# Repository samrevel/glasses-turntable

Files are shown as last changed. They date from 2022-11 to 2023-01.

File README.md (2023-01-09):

# glasses-turntable
This repository has the code, schematic, board. etc for the electronics of the glasses turntable kiosk display in Revel Digital warehouse 13.

The glasses turntable electronics board (board) uses a ATmega8 microcontroller to controll a H bridge that controlls a brushed DC motor. The DC motor has a gear boc to slow the motor down and to increase torqu. The motor turns the whole display. The display is ran from a 12V dc source and is fused. All the logic on the board is running 5V.

On the board there are connector for LEDs (12V LED string), power (2.1X5.5mm barrel jack center positive 12V), homing switch, extranal button (not used), mbrushed DC motor, serial, programmer conncetor, and fan (12V power out, not used). 

The display will rotate when the board recives a serial command. There serial commands are sent by a display located need the glasses turntable. When the board recives a command it will return the same serial command back.

Serial settings:
- Buad: 9600
- Bits: 8
- Stop Bits: 1
- Parity: None
- Flow Control: None
- Data format: ASCII
- Ending charachers: None (will not hurt if send it)

Serial commands (in ASCII):
- "1" rotate to side 1
- "2" rotate to side 2
- "3" rotate to side 3
- "4" rotate for about a second
- "5" rotate for about a second backwares
- "6" rotate for about a haft second
- "7" rotate for about a haft backwares

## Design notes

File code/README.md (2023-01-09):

This the code for the glasses turntable. The code is for the ATmega8 microcontroller located on the PCB. The ATmega8 is running at 8MHz using a extranl resonator.

The code was writen as a PlatformIO project written all in C with no frameworks. Located here is the soucre folder with the code and the PlatformIO Project Configuration File.

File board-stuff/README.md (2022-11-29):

This is all the file that is use to design the electrionics. Everything was make using KiCad and left all the KiCad project file. 
There is also a PDF of the schematic so you can look at it if you dont have KiCad. There are the PCB gerber files too.

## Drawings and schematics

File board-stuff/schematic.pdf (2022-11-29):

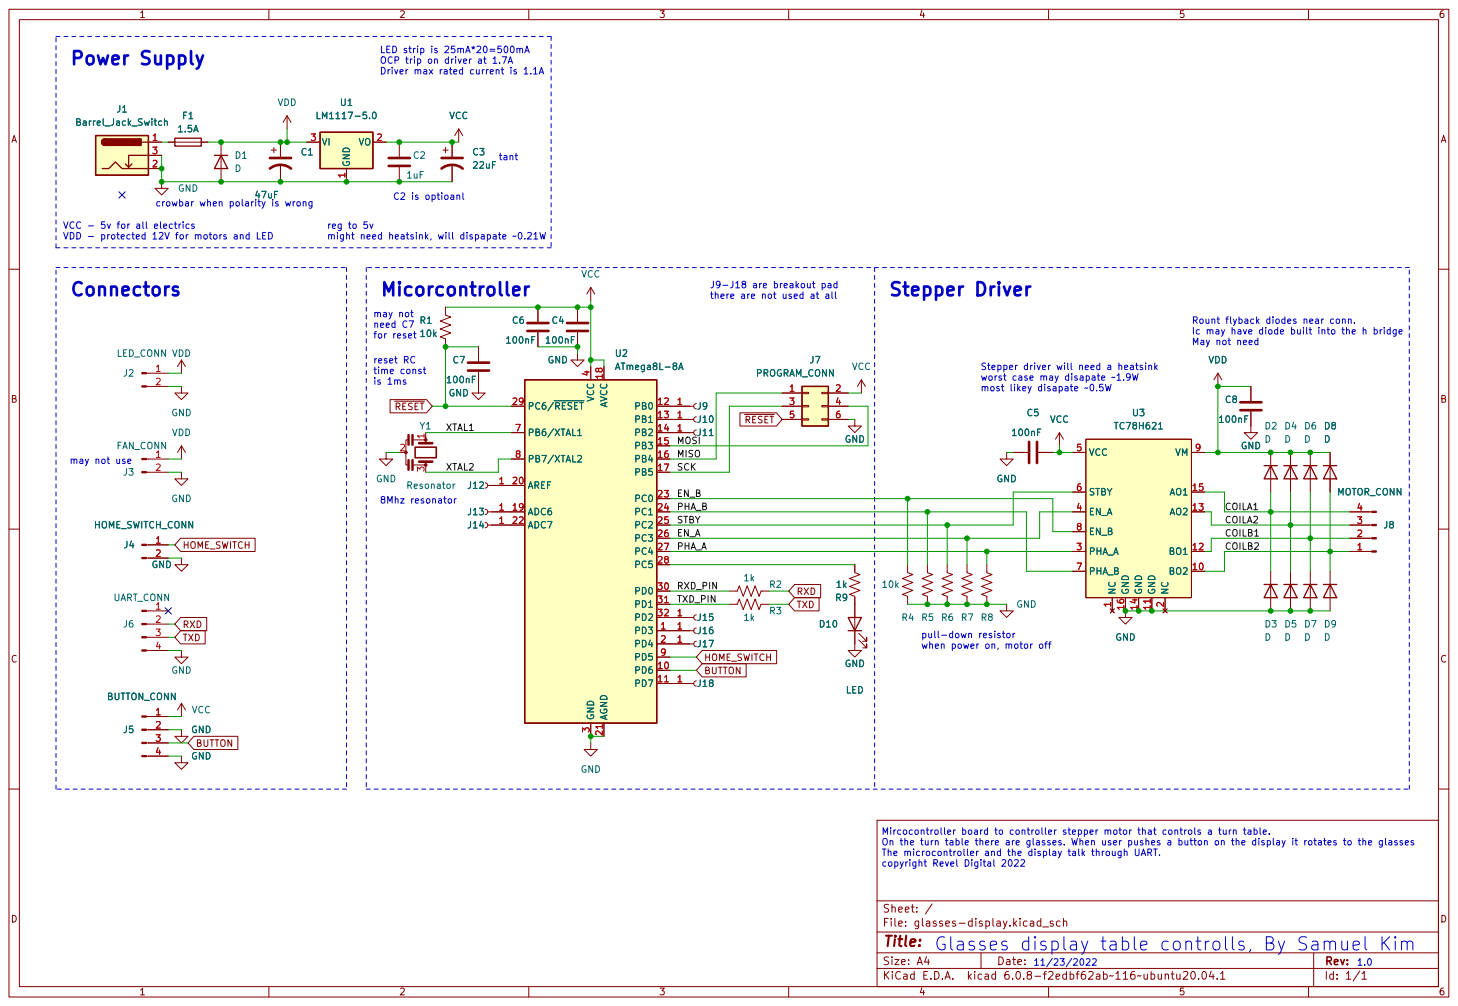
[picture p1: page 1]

for reset LED strip is 25mA*20=500mA
OCP trip on driver at 1.7A Driver max rated current is 1.1A
LM1117-5.0 GND

crowbar when polarity is wrong

VCC - 5v for all electrics VDD - protected 12V for motors and LED

reg to 5v
might need heatsink, will dispapate ~0.21W

1.0 Stepper Driver J9-J18 are breakout pad

Rount flyback diodes near conn. Ic may have diode built into the h bridge VDD

worst case may disapate ~1.9W
most likey disapate ~0.5W

2 PHA_A 3 EN_A 4 VCC 5 STBY 6 PHA_B 7 EN_B 8 VM 9 U3 TC78H621 VCC GND

2 PHA_A 3 EN_A 4 VCC 5 STBY 6 PHA_B 7 EN_B 8 VM 9 GND

1 BO2 10 GND 11 BO1 12 AO2 13 GND 14 AO1 15 GND 16 NC

pull-down resistor
when power on, motor off 11/23/2022 Glasses display table controlls, By Samuel Kim

On the turn table there are glasses. When user pushes a button on the display it rotates to the glasses
The microcontroller and the display talk through UART.
copyright Revel Digital 2022

File: glasses-display.kicad_sch Sheet: /
Id: 1/1 Title:

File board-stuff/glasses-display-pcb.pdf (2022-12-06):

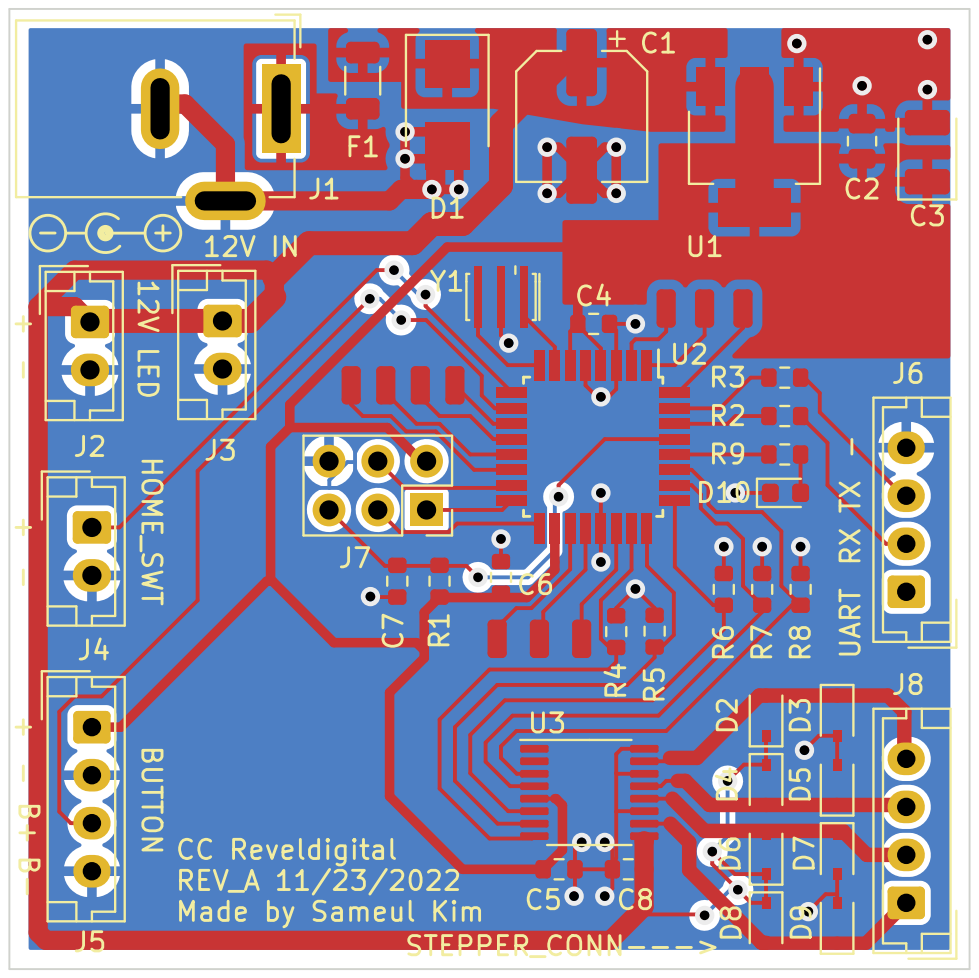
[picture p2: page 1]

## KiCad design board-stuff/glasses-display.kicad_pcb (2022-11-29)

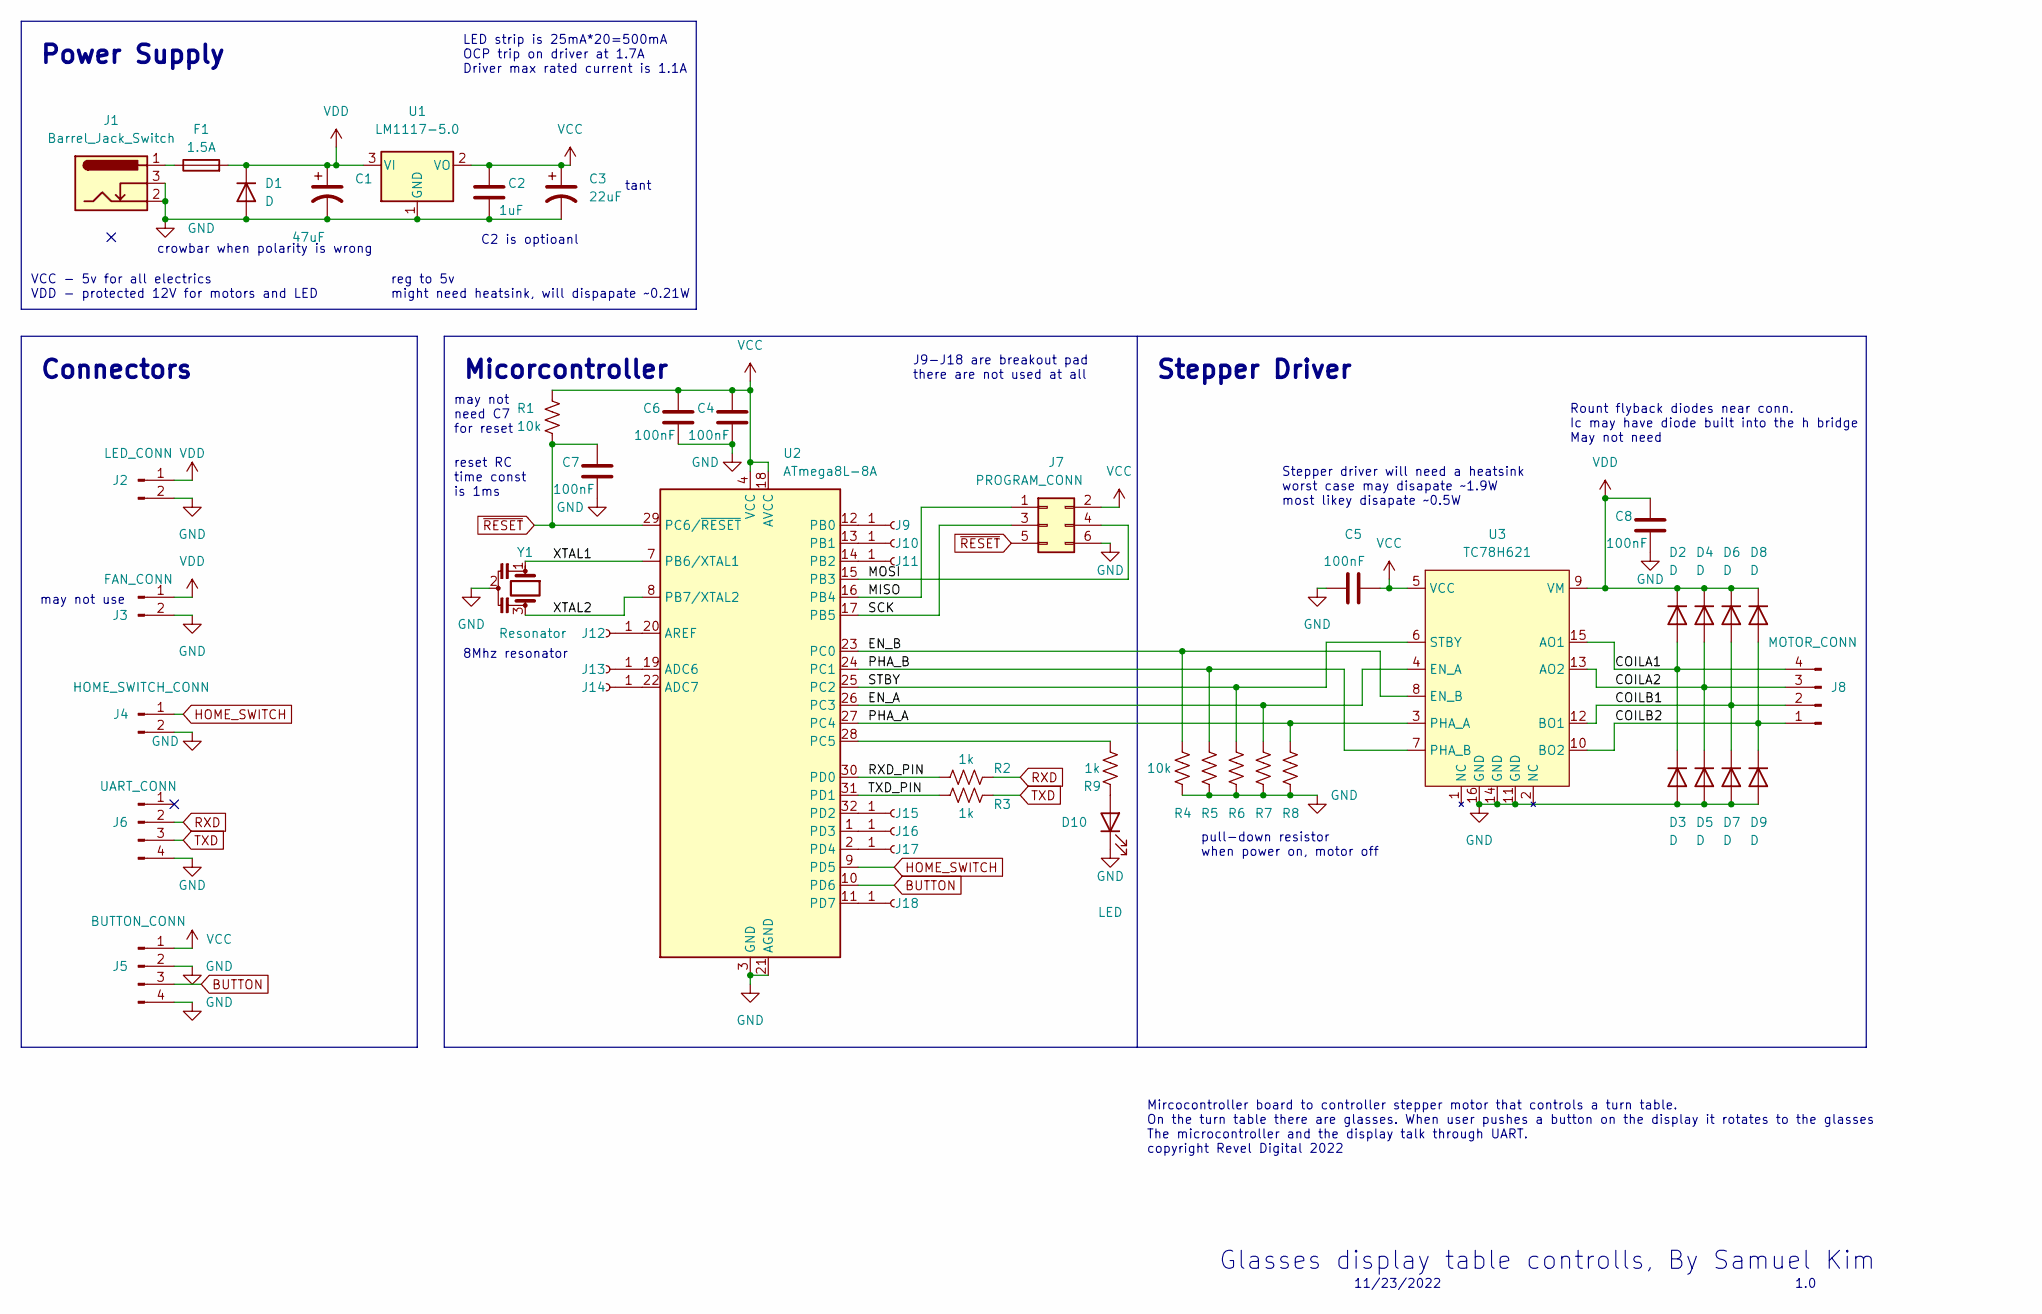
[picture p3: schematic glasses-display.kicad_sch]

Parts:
C1: 47uF; CP_Elec_6.3x5.2
C2: 1uF; R_0805_2012Metric
C3: 22uF; CP_EIA-3528-12_Kemet-T
C4, C5, C6, C7, C8: 100nF; R_0603_1608Metric
D1: D; D_SMB
D2, D3, D4, D5, D6, D7, D8, D9: D; D_SOD-323
D10: LED; LED_0603_1608Metric
F1: 1.5A; R_1206_3216Metric
J1: Barrel_Jack_Switch; BarrelJack_GCT_DCJ200-10-A_Horizontal
J2: LED_CONN; JST_EH_B2B-EH-A_1x02_P2.50mm_Vertical
J3: FAN_CONN; JST_EH_B2B-EH-A_1x02_P2.50mm_Vertical
J4: HOME_SWITCH_CONN; JST_EH_B2B-EH-A_1x02_P2.50mm_Vertical
J5: BUTTON_CONN; JST_EH_B4B-EH-A_1x04_P2.50mm_Vertical
J6: UART_CONN; JST_EH_B4B-EH-A_1x04_P2.50mm_Vertical
J7: PROGRAM_CONN; PinSocket_2x03_P2.54mm_Vertical
J8: MOTOR_CONN; JST_EH_B4B-EH-A_1x04_P2.50mm_Vertical
J9, J10, J11, J12, J13, J14, J15, J16, J17, J18: PAD; SolderWirePad_1x01_SMD_1x2mm
R1, R4, R5, R6, R7, R8: 10k; R_0603_1608Metric
R2, R3, R9: 1k; R_0603_1608Metric
U1: LM1117-5.0; SOT-223-3_TabPin2
U2: ATmega8L-8A; TQFP-32_7x7mm_P0.8mm
U3: TC78H621; TSSOP-16_4.4x5mm_P0.65mm
Y1: Resonator; Resonator_SMD_Murata_CSTxExxV-3Pin_3.0x1.1mm_HandSoldering

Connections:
/COILA1: D2.2 (A), D3.1 (K), J8.4, U3.15 (AO1)
/COILA2: D4.2 (A), D5.1 (K), J8.3, U3.13 (AO2)
/COILB1: D6.2 (A), D7.1 (K), J8.2, U3.12 (BO1)
/COILB2: D8.2 (A), D9.1 (K), J8.1, U3.10 (BO2)
/EN_A: R7.1, U2.26 (PC3), U3.4 (EN_A)
/EN_B: R4.1, U2.23 (PC0), U3.8 (EN_B)
/MISO: J7.1, U2.16 (PB4)
/MOSI: J7.4, U2.15 (PB3)
/PHA_A: R8.1, U2.27 (PC4), U3.3 (PHA_A)
/PHA_B: R5.1, U2.24 (PC1), U3.7 (PHA_B)
/RXD_PIN: R2.1, U2.30 (PD0)
/SCK: J7.3, U2.17 (PB5)
/STBY: R6.1, U2.25 (PC2), U3.6 (STBY)
/TXD_PIN: R3.1, U2.31 (PD1)
/XTAL1: U2.7 (PB6/XTAL1), Y1.1
/XTAL2: U2.8 (PB7/XTAL2), Y1.3
BUTTON: J5.3, U2.10 (PD6)
GND: C1.2, C2.2, C3.2, C4.2, C5.1, C6.2, C7.2, C8.2, D1.2 (A), D3.2 (A), D5.2 (A), D7.2 (A), D9.2 (A), D10.1 (K), J1.2, J1.3, J2.2, J3.2, J4.2, J5.2, J5.4, J6.4, J7.6, R4.2, R5.2, R6.2, R7.2, R8.2, U1.1 (GND), U2.3 (GND), U2.5 (GND), U2.21 (AGND), U3.11 (GND), U3.14 (GND), U3.16 (GND), Y1.2
HOME_SWITCH: J4.1, U2.9 (PD5)
unnamed: D10.2 (A), R9.2
unnamed: F1.1, J1.1
unnamed: J9.1, U2.12 (PB0)
unnamed: J10.1, U2.13 (PB1)
unnamed: J11.1, U2.14 (PB2)
unnamed: J12.1, U2.20 (AREF)
unnamed: J13.1, U2.19 (ADC6)
unnamed: J14.1, U2.22 (ADC7)
unnamed: J15.1, U2.32 (PD2)
unnamed: J16.1, U2.1 (PD3)
unnamed: J17.1, U2.2 (PD4)
unnamed: J18.1, U2.11 (PD7)
unnamed: R9.1, U2.28 (PC5)
RXD: J6.2, R2.2
TXD: J6.3, R3.2
VCC: C2.1, C3.1, C4.1, C5.2, C6.1, J5.1, J7.2, R1.1, U1.2 (VO), U2.4 (VCC), U2.6 (VCC), U2.18 (AVCC), U3.5 (VCC)
VDD: C1.1, C8.1, D1.1 (K), D2.1 (K), D4.1 (K), D6.1 (K), D8.1 (K), F1.2, J2.1, J3.1, U1.3 (VI), U3.9 (VM)
~RESET: C7.1, J7.5, R1.2, U2.29 (PC6/~RESET)

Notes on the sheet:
may not need C7 for reset
C2 is optioanl
crowbar when polarity is wrong
Stepper driver will need a heatsink worst case may disapate ~1.9W most likey disapate ~0.5W
reset RC time const is 1ms
reg to 5v might need heatsink, will dispapate ~0.21W
LED strip is 25mA*20=500mA OCP trip on driver at 1.7A Driver max rated current is 1.1A
8Mhz resonator
pull-down resistor when power on, motor off
J9-J18 are breakout pad there are not used at all
11/23/2022
Mircocontroller board to controller stepper motor that controls a turn table. On the turn table there are glasses. When user pushes a button on the display it rotates to the glasses The microcontroller and the display talk through UART. copyright Revel Digital 2022
1.0
Glasses display table controlls, By Samuel Kim
Micorcontroller
may not use
tant
Connectors
Stepper Driver
VCC - 5v for all electrics VDD - protected 12V for motors and LED
Rount flyback diodes near conn. Ic may have diode built into the h bridge May not need
Power Supply

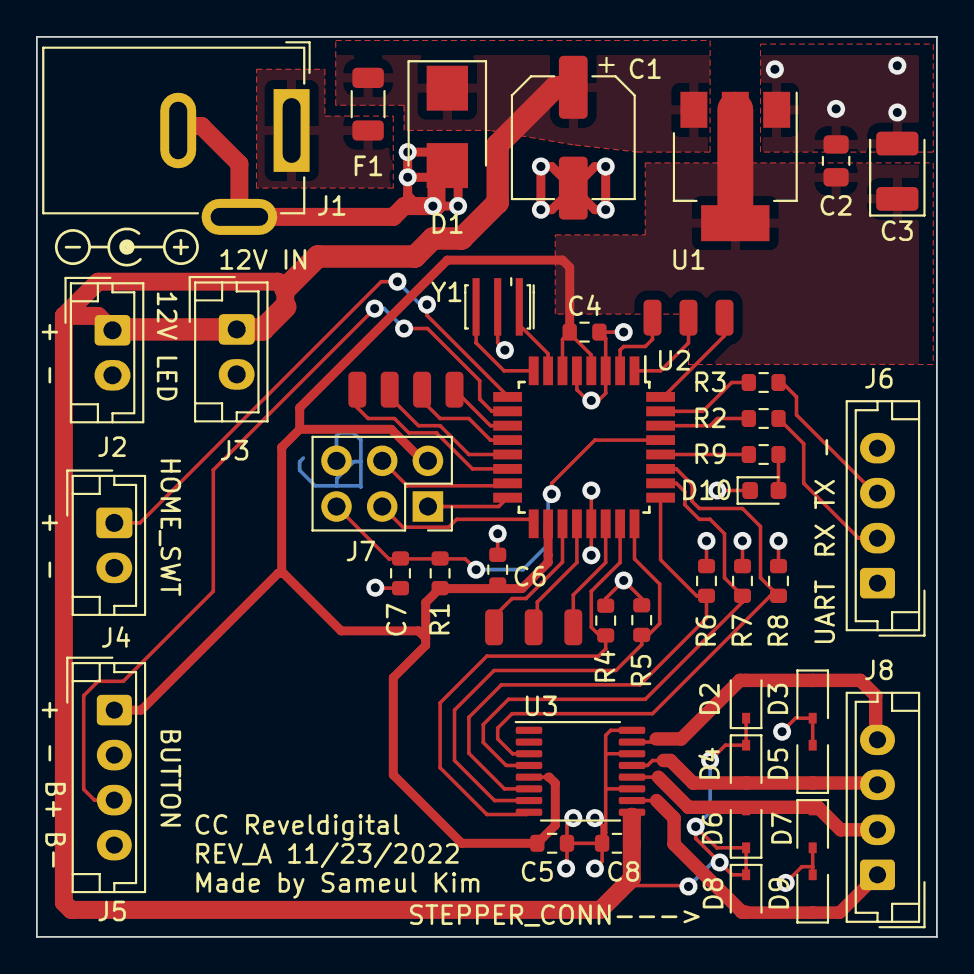
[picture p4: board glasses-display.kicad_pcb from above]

Board: 2 copper layers, 50.0 x 50.0 mm, 50 parts (0 on the bottom side), 37 nets.

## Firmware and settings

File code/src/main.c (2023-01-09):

// using the atmega8l microcontroller
// Datasheet: http://ww1.microchip.com/downloads/en/DeviceDoc/atmel-2486-8-bit-avr-microcontroller-atmega8_l_datasheet.pdf
// dual brushed dc motor/stepper driver chip is TC78H621FNG
// Datasheet: https://toshiba.semicon-storage.com/info/TC78H621FNG_datasheet_en_20170410.pdf?did=57992&prodName=TC78H621FNG

#include <avr/io.h>
#include <util/delay.h>
#include <stdbool.h> // i want to use bool
#define byte uint8_t // i like using byte, i can remeber what it is

// ------------ PINS --------------------------
// all pins for the motor H-brigde driver is connected to port C
// this is using
// PC0 - EN_B, PC3 - EN_A
// PC1 - PHA_B, PC4 - PHA_A
// PC2 - STBY, PC5 - LED
// motor B is not used
#define MPORT PORTC
#define MPORTD DDRC
#define EN_B 0b00000001
#define EN_A 0b00001000
#define PHA_B 0b00000010
#define PHA_A 0b00010000
#define STBY 0b00000100
#define LED 0b00100000

// Inputs
// PD6 - BUTTON (need pullup res)
// PD5 - HOME_SWITCH (need pullup res)
// PD0 - RXD, PD1 - TXD
#define BUTTON 0b01000000
#define HOME_SWITCH 0b00100000

// motor speed
// degs is calc with the motor speed of 40rpm
#define DELAY_START 100
#define DELAY_360D 1500
#define DELAY_180D 750
#define DELAY_120D 500
#define DELAY_EX1 125 // adjust the delay to account for the insersha of the turntable and gearbox ans stop speed
#define DELAY_EX2 150 // adjust the delay to account for the insersha
#define DELAY_EX3 100 // adjust the delay to account for the insersha
#define DELAY_240D 1000
#define DELAY_STOP 0 // not driving motor backware to stop it

// Set up serial
#define FOSC F_CPU // Clock Speed, 8MHz extranal
#define BAUD 9600
#define MYUBRR FOSC / 16 / BAUD - 1

// DDRx   - Used to configure the respective PORT as output/input
// PORTx  - Used to write the data to the Port pins
// PINx   - Used to Read the data from the port pins

// init serial func, right from the datasheet page 135
void USART_Init(unsigned int ubrr)
{
  /* Set baud rate */
  UBRRH = (unsigned char)(ubrr >> 8);
  UBRRL = (unsigned char)ubrr;
  /* Enable receiver and transmitter */
  UCSRB = (1 << RXEN) | (1 << TXEN);
  /* Set frame format: 8data, 1stop bit */
  UCSRC = (1 << URSEL) | /* (1 << USBS) |*/ (3 << UCSZ0);
}

// serial receive func, right from the datasheet page 139
unsigned char USART_Receive(void) // may change to return byte instead of char, makes things ez later
{
  /* Wait for data to be received */
  while (!(UCSRA & (1 << RXC)))
    ;
  /* Get and return received data from buffer */
  return UDR;
}

// serial printing, just for testing
void USART_Transmit(unsigned char data)
{
  /* Wait for empty transmit buffer */
  while (!(UCSRA & (1 << UDRE)))
    ;
  /* Put data into buffer, sends the data */
  UDR = data;
}

// this function rotoates the motor
// int delay - runs the motor for the number of ms, negitive numbers rotate backware
// bool home - when true the motor stops when it gets a home trigger, false will ignor the home trigger
// bool slow - when true the motor runs at 50% duly at 500 hz, false the motor runs normal.
void rotate(int delay, bool home, bool slow)
{
  // turn off motor
  if (delay == 0)
  {
    PORTC = 0;
    return;
  }

  if (delay > 0)
  {
    PORTC = (EN_A | STBY | LED);
    for (int i = 0; i < delay; i++)
    {
      _delay_ms(1); // delay to let motor run
      if (slow)
      {
        PORTC = PORTC ^ EN_A;
      }

      if (home)
      {
        if (!(PIND & (HOME_SWITCH))) // check to see if it is homes
        {
          PORTC = 0; // turn off motor
          return;    // when the HOME_SWITCH goes low (when it is pressed). it will break out of for loop
        }
      }
    }
  }
  else
  {
    PORTC = (EN_A | STBY | LED | PHA_A);
    for (int i = 0; i > delay; i--)
    {
      _delay_ms(1); // delay to let motor run
      if (slow)
      {
        PORTC = PORTC ^ EN_A;
      }
      if (home)
      {
        if (!(PIND & (HOME_SWITCH))) // check to see if it is homes
        {
          PORTC = 0;
          return; // when the HOME_SWITCH goes low (when it is pressed). it will break out of for loop
        }
      }
    }
  }
  PORTC = 0; // turn off the motor
  return;
}

int main()
{
  //  set motor pins as outputs
  DDRC = 0b00111111;
  // turn off all motor pins
  PORTC = 0b00000000;

  // enable inputs as inputs
  DDRD = 0b00000000;
  // enable pullup resistors
  PORTD = (BUTTON | HOME_SWITCH);

  // init serial
  USART_Init(MYUBRR);
  // rotate(-1,1,1);

  while (1)
  {

    switch (USART_Receive())
    {
    case '\n': // ingor termiator chars
    case '\r':
      break;
    case '1': // rotate to side 1
      USART_Transmit('1');
      if (!(PIND & (HOME_SWITCH))) // when home switch is low, that means it is homed
      {
        rotate(DELAY_180D, false, false); // rotate out of the way of the
      }
      rotate(DELAY_START + DELAY_360D, true, false); // find where home is
      rotate(DELAY_180D, false, false);              // move more to home a 2nd time
      rotate(DELAY_360D, true, false);               // find where home is
      rotate(DELAY_EX1, false, false);               // rotate to the right side
      // rotate(DELAY_STOP, false, false); // stop motor
      PORTC = 0; // turn off motor
      break;
    case '2': // rotate to side 2
      USART_Transmit('2');
      if (!(PIND & (HOME_SWITCH))) // when home switch is low, that means it is homed
      {
        rotate(DELAY_180D, false, false); // go backwares to get more persice position of the home
      }
      rotate(DELAY_START + DELAY_360D, true, false); // find where home is
      rotate(DELAY_180D, false, false);              // move more to home a 2nd time
      rotate(DELAY_360D, true, false);               // find where home is
      rotate(DELAY_120D + DELAY_EX2, false, false);  // move to the right side of the display
      // rotate(DELAY_STOP, false, false); // stop motor
      PORTC = 0; // turn off motor
      break;
    case '3': // rotate to side 3
      USART_Transmit('3');
      if (!(PIND & (HOME_SWITCH))) // when home switch is low, that means it is homed
      {
        rotate(DELAY_180D, false, false); // go backwares to get more persice position of the home
      }
      rotate(DELAY_START + DELAY_360D, true, false); // find where home is
      rotate(DELAY_180D, false, false);              // move more to home a 2nd time
      rotate(DELAY_360D, true, false);               // find where home is
      rotate(DELAY_240D + DELAY_EX3, false, false);  // move to the right side of the display
      // rotate(DELAY_STOP, false, false); // stop motor
      PORTC = 0; // turn off motor
      break;
    case '4': // rotate forward for 500ms
      USART_Transmit('4');
      rotate(500, false, false);
      PORTC = 0; // turn off motor
      break;
    case '5': // rotate backwares for 500ms
      USART_Transmit('5');
      rotate(-500, false, false);
      PORTC = 0; // turn off motor
      break;
    case '6': // rotate forward for 250ms
      USART_Transmit('6');
      rotate(250, false, false);
      PORTC = 0; // turn off motor
      break;
    case '7': // rotate backwares for 250ms
      USART_Transmit('7');
      rotate(-250, false, false);
      PORTC = 0; // turn off motor
      break;
    case '8':
      USART_Transmit('8');
      PORTC = 0; // turn off motor
      break;
    default:
      break;
    }
  }
}
